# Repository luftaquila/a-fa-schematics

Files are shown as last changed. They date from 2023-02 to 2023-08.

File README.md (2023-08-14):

# E-Formula 전기시스템 파트 회로도 / PCB / 배선

상위 프로젝트: [luftaquila/a-fa-landing](https://github.com/luftaquila/a-fa-landing)



* 회로도  
    * *EV.kicad_pro*  
       * KiCAD 6.0 프로젝트  
       * 메인 회로도입니다. 추상적으로 차량의 모든 고전압/저전압 전기 계통이 표현되어 있습니다. 메인 회로도 하위의 계층 회로도는 개별 구성 요소를 추상화합니다. 계층 회로도 중 `/PCB` 폴더 하위의 파일들은 실제 PCB의 회로도입니다.

* PCB  
    * */PCB/\*.kicad_pcb*  
       * KiCAD 6.0 PCB 아트워크  
       * 각 PCB 폴더는 하나의 독립적인 KiCAD 프로젝트입니다. 메인 회로도인 `EV.kicad_sch` 파일이 계층 회로 구성을 통해 각 PCB 폴더의 `*.kicad_sch` 파일을 가리키는 방식으로 서로 연결되어 있습니다.

* 배선  
    * *wirings*
       * 차량의 모든 외부 배선을 표현하는 [WireViz](https://github.com/formatc1702/WireViz) 배선 체계도입니다.

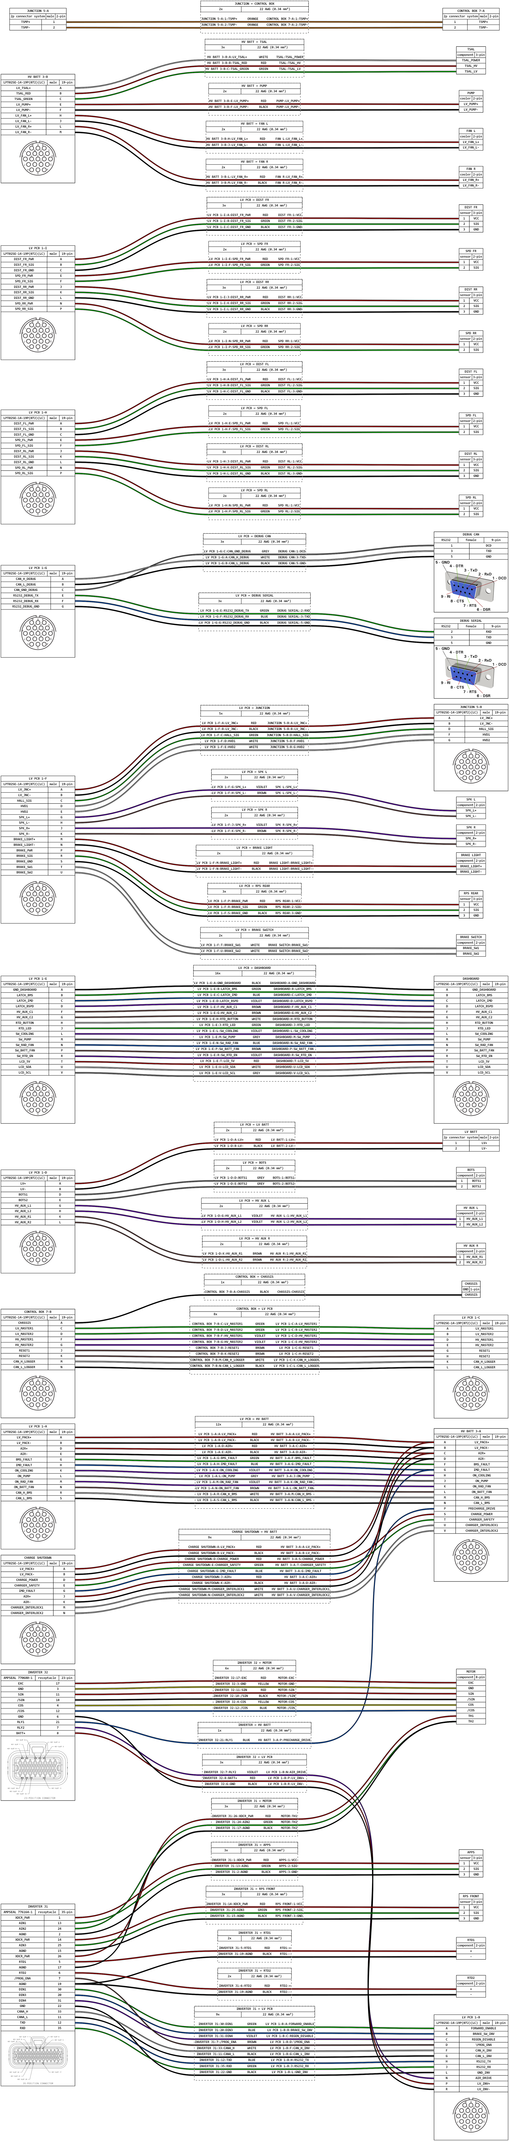
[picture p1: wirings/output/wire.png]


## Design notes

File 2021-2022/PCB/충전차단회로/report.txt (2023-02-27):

정보: 'C:\Users\kbc9513\Desktop\충전차단회로\충전차단회로.net' 네트리스트 파일을 읽고 있습니다.

정보: 참조 지정자를 사용하여 심볼과 풋프린트를 일치시킵니다.

정보: 심볼 'R1:Resistor_THT:R_Axial_DIN0207_L6.3mm_D2.5mm_P10.16mm_Horizontal' 처리 중입니다.
정보: 심볼 'R2:Resistor_THT:R_Axial_DIN0207_L6.3mm_D2.5mm_P10.16mm_Horizontal' 처리 중입니다.
정보: 심볼 'R3:Resistor_THT:R_Axial_DIN0207_L6.3mm_D2.5mm_P10.16mm_Horizontal' 처리 중입니다.
정보: 심볼 'D6:LED_THT:LED_D5.0mm' 처리 중입니다.
정보: 심볼 'J2:LED_THT:LED_D5.0mm' 처리 중입니다.
정보: 심볼 'R4:Resistor_THT:R_Axial_DIN0207_L6.3mm_D2.5mm_P10.16mm_Horizontal' 처리 중입니다.
정보: 심볼 'J3:LED_THT:LED_D5.0mm' 처리 중입니다.
정보: 심볼 'D3:LED_THT:LED_D5.0mm' 처리 중입니다.
정보: 심볼 'U1:Goolgle_Drive_Library:ADJ14012' 처리 중입니다.
정보: 심볼 'J1:LED_THT:LED_D5.0mm' 처리 중입니다.
정보: 심볼 'U2:Goolgle_Drive_Library:ADJ14012' 처리 중입니다.
정보: 심볼 'D1:Diode_THT:D_DO-15_P10.16mm_Horizontal' 처리 중입니다.
정보: 심볼 'D2:Diode_THT:D_DO-15_P10.16mm_Horizontal' 처리 중입니다.
정보: 심볼 'D4:Diode_THT:D_DO-15_P10.16mm_Horizontal' 처리 중입니다.
정보: 심볼 'D5:Diode_THT:D_DO-15_P10.16mm_Horizontal' 처리 중입니다.
정보: 심볼 'J4:Connector_Wire:SolderWire-0.75sqmm_1x02_P4.8mm_D1.25mm_OD2.3mm' 처리 중입니다.
정보: 심볼 'J5:Connector_JST:JST_EH_B10B-EH-A_1x10_P2.50mm_Vertical' 처리 중입니다.
네트 Net-(R1-Pad2)을(를) 추가합니다.
R1 핀 2을(를) Net-(R1-Pad2)에 연결했습니다.
R2이(가) 추가되었습니다 (풋프린트 'Resistor_THT:R_Axial_DIN0207_L6.3mm_D2.5mm_P10.16mm_Horizontal').
참조 지정자 REF**을(를) R2(으)로 변경하였습니다.
값 R2을(를) R_Axial_DIN0207_L6.3mm_D2.5mm_P10.16mm_Horizontal에서 500(으)로 변경하였습니다.
R2 심볼 관련성을 에서 /9cac4b8f-fc90-46aa-9ba6-c3c9f12e7e00(으)로 업데이트하였습니다.
R2 속성이 업데이트되었습니다.
네트 GND을(를) 추가합니다.
R2 핀 1을(를) GND에 연결했습니다.
R2 핀 2을(를) Net-(D3-Pad2)에 연결했습니다.
R3이(가) 추가되었습니다 (풋프린트 'Resistor_THT:R_Axial_DIN0207_L6.3mm_D2.5mm_P10.16mm_Horizontal').
참조 지정자 REF**을(를) R3(으)로 변경하였습니다.
값 R3을(를) R_Axial_DIN0207_L6.3mm_D2.5mm_P10.16mm_Horizontal에서 1.5k(으)로 변경하였습니다.
R3 심볼 관련성을 에서 /c4ed5e0d-1470-49a7-b4d8-6793531b15c6(으)로 업데이트하였습니다.
R3 속성이 업데이트되었습니다.
네트 Net-(D6-Pad2)을(를) 추가합니다.
R3 핀 1을(를) Net-(D6-Pad2)에 연결했습니다.
네트 Net-(R3-Pad2)을(를) 추가합니다.
R3 핀 2을(를) Net-(R3-Pad2)에 연결했습니다.
R4이(가) 추가되었습니다 (풋프린트 'Resistor_THT:R_Axial_DIN0207_L6.3mm_D2.5mm_P10.16mm_Horizontal').
참조 지정자 REF**을(를) R4(으)로 변경하였습니다.
값 R4을(를) R_Axial_DIN0207_L6.3mm_D2.5mm_P10.16mm_Horizontal에서 500(으)로 변경하였습니다.
R4 심볼 관련성을 에서 /f852aa6c-fee4-4d12-afd9-4db3451e35ae(으)로 업데이트하였습니다.
R4 속성이 업데이트되었습니다.
R4 핀 1을(를) GND에 연결했습니다.
R4 핀 2을(를) Net-(D6-Pad2)에 연결했습니다.
D3이(가) 추가되었습니다 (풋프린트 'LED_THT:LED_D5.0mm').
참조 지정자 REF**을(를) D3(으)로 변경하였습니다.
값 D3을(를) LED_D5.0mm에서 LED(으)로 변경하였습니다.
D3 심볼 관련성을 에서 /42a2bed2-408c-4340-bf5e-717f9ef794f6(으)로 업데이트하였습니다.
D3 속성이 업데이트되었습니다.
D3 핀 1을(를) GND에 연결했습니다.
D3 핀 2을(를) Net-(D3-Pad2)에 연결했습니다.
D6이(가) 추가되었습니다 (풋프린트 'LED_THT:LED_D5.0mm').
참조 지정자 REF**을(를) D6(으)로 변경하였습니다.
값 D6을(를) LED_D5.0mm에서 LED(으)로 변경하였습니다.
D6 심볼 관련성을 에서 /54d4ccdd-eadf-48c0-9c4d-c1c9c0573c55(으)로 업데이트하였습니다.
D6 속성이 업데이트되었습니다.
D6 핀 1을(를) GND에 연결했습니다.
D6 핀 2을(를) Net-(D6-Pad2)에 연결했습니다.
J1이(가) 추가되었습니다 (풋프린트 'LED_THT:LED_D5.0mm').
참조 지정자 REF**을(를) J1(으)로 변경하였습니다.
값 J1을(를) LED_D5.0mm에서 Push-Rotate(으)로 변경하였습니다.
J1 심볼 관련성을 에서 /b73f0b34-054d-4499-b93b-f1d81da21695(으)로 업데이트하였습니다.
J1 속성이 업데이트되었습니다.
네트 Net-(J1-Pad1)을(를) 추가합니다.
J1 핀 1을(를) Net-(J1-Pad1)에 연결했습니다.
네트 CHARGE_POWER을(를) 추가합니다.
J1 핀 2을(를) CHARGE_POWER에 연결했습니다.
J2이(가) 추가되었습니다 (풋프린트 'LED_THT:LED_D5.0mm').
참조 지정자 REF**을(를) J2(으)로 변경하였습니다.
값 J2을(를) LED_D5.0mm에서 Charging_Interlock(으)로 변경하였습니다.
J2 심볼 관련성을 에서 /5271f79e-a5a9-419a-907c-0455a139a4e2(으)로 업데이트하였습니다.
J2 속성이 업데이트되었습니다.
네트 Net-(J2-Pad1)을(를) 추가합니다.
J2 핀 1을(를) Net-(J2-Pad1)에 연결했습니다.
J2 핀 2을(를) Net-(J1-Pad1)에 연결했습니다.
J3이(가) 추가되었습니다 (풋프린트 'LED_THT:LED_D5.0mm').
참조 지정자 REF**을(를) J3(으)로 변경하였습니다.
값 J3을(를) LED_D5.0mm에서 reset(으)로 변경하였습니다.
J3 심볼 관련성을 에서 /431705a8-970b-4ff5-b043-d4baa9fe7a97(으)로 업데이트하였습니다.
J3 속성이 업데이트되었습니다.
네트 Reset_Button을(를) 추가합니다.
J3 핀 1을(를) Reset_Button에 연결했습니다.
J3 핀 2을(를) GND에 연결했습니다.
U1이(가) 추가되었습니다 (풋프린트 'Goolgle_Drive_Library:ADJ14012').
참조 지정자 REF**을(를) U1(으)로 변경하였습니다.
값 U1을(를) RELAY_ADJ_1C_PAN에서 ADJ14012(으)로 변경하였습니다.
U1 심볼 관련성을 에서 /4dad1e6b-5c80-4c11-8ad5-7b16562ecc74(으)로 업데이트하였습니다.
U1 속성이 업데이트되었습니다.
U1 핀 1을(를) CHARGE_POWER에 연결했습니다.
네트 IMD_FAULT을(를) 추가합니다.
U1 핀 9을(를) IMD_FAULT에 연결했습니다.
U1 핀 8을(를) Reset_Button에 연결했습니다.
네트 Net-(U1-Pad2)을(를) 추가합니다.
U1 핀 2을(를) Net-(U1-Pad2)에 연결했습니다.
U1 핀 6을(를) Net-(R1-Pad2)에 연결했습니다.
U1 핀 4을(를) Net-(J2-Pad1)에 연결했습니다.
R1이(가) 추가되었습니다 (풋프린트 'Resistor_THT:R_Axial_DIN0207_L6.3mm_D2.5mm_P10.16mm_Horizontal').
U2이(가) 추가되었습니다 (풋프린트 'Goolgle_Drive_Library:ADJ14012').
참조 지정자 REF**을(를) U2(으)로 변경하였습니다.
값 U2을(를) RELAY_ADJ_1C_PAN에서 ADJ14012(으)로 변경하였습니다.
U2 심볼 관련성을 에서 /b592de20-0538-4c3f-838d-1e2c5cb1cc5b(으)로 업데이트하였습니다.
U2 속성이 업데이트되었습니다.
U2 핀 1을(를) CHARGE_POWER에 연결했습니다.
네트 CHARGE_SAFETY을(를) 추가합니다.
U2 핀 9을(를) CHARGE_SAFETY에 연결했습니다.
U2 핀 8을(를) Reset_Button에 연결했습니다.
네트 AIR+_ACTIVE을(를) 추가합니다.
U2 핀 2을(를) AIR+_ACTIVE에 연결했습니다.
U2 핀 6을(를) Net-(R3-Pad2)에 연결했습니다.
U2 핀 4을(를) Net-(U1-Pad2)에 연결했습니다.
참조 지정자 REF**을(를) R1(으)로 변경하였습니다.
D1이(가) 추가되었습니다 (풋프린트 'Diode_THT:D_DO-15_P10.16mm_Horizontal').
참조 지정자 REF**을(를) D1(으)로 변경하였습니다.
값 D1을(를) D_DO-15_P10.16mm_Horizontal에서 1N4001(으)로 변경하였습니다.
D1 심볼 관련성을 에서 /04f6e974-f1aa-4eba-86e4-b6ef5f9aab0c(으)로 업데이트하였습니다.
D1 속성이 업데이트되었습니다.
D1 핀 1을(를) CHARGE_POWER에 연결했습니다.
D1 핀 2을(를) Reset_Button에 연결했습니다.
값 R1을(를) R_Axial_DIN0207_L6.3mm_D2.5mm_P10.16mm_Horizontal에서 1.5k(으)로 변경하였습니다.
D2이(가) 추가되었습니다 (풋프린트 'Diode_THT:D_DO-15_P10.16mm_Horizontal').
참조 지정자 REF**을(를) D2(으)로 변경하였습니다.
값 D2을(를) D_DO-15_P10.16mm_Horizontal에서 1N4001(으)로 변경하였습니다.
D2 심볼 관련성을 에서 /54878bf1-8f32-4bae-9656-436220390256(으)로 업데이트하였습니다.
D2 속성이 업데이트되었습니다.
D2 핀 1을(를) CHARGE_POWER에 연결했습니다.
D2 핀 2을(를) IMD_FAULT에 연결했습니다.
R1 심볼 관련성을 에서 /6292f032-e986-4e86-8de2-ea34f8531d00(으)로 업데이트하였습니다.
D4이(가) 추가되었습니다 (풋프린트 'Diode_THT:D_DO-15_P10.16mm_Horizontal').
참조 지정자 REF**을(를) D4(으)로 변경하였습니다.
값 D4을(를) D_DO-15_P10.16mm_Horizontal에서 1N4001(으)로 변경하였습니다.
D4 심볼 관련성을 에서 /92f338f3-3812-48b7-a538-72a2acf5d354(으)로 업데이트하였습니다.
D4 속성이 업데이트되었습니다.
D4 핀 1을(를) CHARGE_POWER에 연결했습니다.
D4 핀 2을(를) Reset_Button에 연결했습니다.
R1 속성이 업데이트되었습니다.
D5이(가) 추가되었습니다 (풋프린트 'Diode_THT:D_DO-15_P10.16mm_Horizontal').
참조 지정자 REF**을(를) D5(으)로 변경하였습니다.
값 D5을(를) D_DO-15_P10.16mm_Horizontal에서 1N4001(으)로 변경하였습니다.
D5 심볼 관련성을 에서 /d5f5c3b9-1b42-4bee-8aa3-7b56f2060ad2(으)로 업데이트하였습니다.
D5 속성이 업데이트되었습니다.
D5 핀 1을(를) CHARGE_POWER에 연결했습니다.
D5 핀 2을(를) CHARGE_SAFETY에 연결했습니다.
네트 Net-(D3-Pad2)을(를) 추가합니다.
J4이(가) 추가되었습니다 (풋프린트 'Connector_Wire:SolderWire-0.75sqmm_1x02_P4.8mm_D1.25mm_OD2.3mm').
참조 지정자 REF**을(를) J4(으)로 변경하였습니다.
값 J4을(를) SolderWire-0.75sqmm_1x02_P4.8mm_D1.25mm_OD2.3mm에서 SMPS INPUT(으)로 변경하였습니다.
J4 심볼 관련성을 에서 /914a5bc4-e45f-4260-9574-6d60e49f788f(으)로 업데이트하였습니다.
J4 속성이 업데이트되었습니다.
J4에 'BOM에서 제외' 제작 속성이 제거되었습니다.
J4 핀 1을(를) CHARGE_POWER에 연결했습니다.
J4 핀 2을(를) GND에 연결했습니다.
R1 핀 1을(를) Net-(D3-Pad2)에 연결했습니다.
J5이(가) 추가되었습니다 (풋프린트 'Connector_JST:JST_EH_B10B-EH-A_1x10_P2.50mm_Vertical').
참조 지정자 REF**을(를) J5(으)로 변경하였습니다.
값 J5을(를) JST_EH_B10B-EH-A_1x10_P2.50mm_Vertical에서 Conn_01x10_Male(으)로 변경하였습니다.
J5 심볼 관련성을 에서 /5f07ac3b-b444-4c3e-bbea-05685bee6cad(으)로 업데이트하였습니다.
J5 속성이 업데이트되었습니다.
J5 핀 1을(를) CHARGE_POWER에 연결했습니다.
J5 핀 2을(를) GND에 연결했습니다.
J5 핀 3을(를) IMD_FAULT에 연결했습니다.
J5 핀 4을(를) AIR+_ACTIVE에 연결했습니다.
J5 핀 5을(를) AIR+_ACTIVE에 연결했습니다.
네트 unconnected-(J5-Pad6)을(를) 추가합니다.
J5 핀 6을(를) unconnected-(J5-Pad6)에 연결했습니다.
네트 unconnected-(J5-Pad7)을(를) 추가합니다.
J5 핀 7을(를) unconnected-(J5-Pad7)에 연결했습니다.
J5 핀 8을(를) CHARGE_POWER에 연결했습니다.
J5 핀 9을(를) CHARGE_SAFETY에 연결했습니다.
J5 핀 10을(를) GND에 연결했습니다.

정보: 총 경고: 0개, 오류: 0개.

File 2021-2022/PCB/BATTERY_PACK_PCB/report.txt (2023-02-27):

1k이(가) R18(으)로 주석 처리되었습니다.
부품 참조번호 주석 처리가 완료되었습니다.

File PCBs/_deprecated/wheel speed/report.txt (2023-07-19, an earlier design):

Info: Processing symbol 'C1:Capacitor_THT:C_Disc_D5.0mm_W2.5mm_P2.50mm'.
Info: Processing symbol 'C2:Capacitor_THT:C_Disc_D5.0mm_W2.5mm_P2.50mm'.
Info: Processing symbol 'C3:Capacitor_THT:C_Disc_D5.0mm_W2.5mm_P2.50mm'.
Info: Processing symbol 'C4:Capacitor_THT:C_Disc_D5.0mm_W2.5mm_P2.50mm'.
Info: Processing symbol 'J1:Connector_PinHeader_2.54mm:PinHeader_1x02_P2.54mm_Vertical'.
Info: Processing symbol 'J2:Connector_PinHeader_2.54mm:PinHeader_1x04_P2.54mm_Vertical'.
Info: Processing symbol 'J3:Connector_PinHeader_2.54mm:PinHeader_1x08_P2.54mm_Vertical'.
Info: Processing symbol 'R1:Resistor_THT:R_Axial_DIN0204_L3.6mm_D1.6mm_P5.08mm_Horizontal'.
Info: Processing symbol 'R2:Resistor_THT:R_Axial_DIN0204_L3.6mm_D1.6mm_P5.08mm_Horizontal'.
Info: Processing symbol 'R3:Resistor_THT:R_Axial_DIN0204_L3.6mm_D1.6mm_P5.08mm_Horizontal'.
Info: Processing symbol 'R4:Resistor_THT:R_Axial_DIN0204_L3.6mm_D1.6mm_P5.08mm_Horizontal'.
Info: Processing symbol 'R5:Resistor_THT:R_Axial_DIN0204_L3.6mm_D1.6mm_P5.08mm_Horizontal'.
Info: Processing symbol 'R6:Resistor_THT:R_Axial_DIN0204_L3.6mm_D1.6mm_P5.08mm_Horizontal'.
Info: Processing symbol 'R7:Resistor_THT:R_Axial_DIN0204_L3.6mm_D1.6mm_P5.08mm_Horizontal'.
Info: Processing symbol 'R8:Resistor_THT:R_Axial_DIN0204_L3.6mm_D1.6mm_P5.08mm_Horizontal'.
Info: Processing symbol 'R9:Resistor_THT:R_Axial_DIN0204_L3.6mm_D1.6mm_P5.08mm_Horizontal'.
Info: Processing symbol 'R10:Resistor_THT:R_Axial_DIN0204_L3.6mm_D1.6mm_P5.08mm_Horizontal'.
Info: Processing symbol 'R11:Resistor_THT:R_Axial_DIN0204_L3.6mm_D1.6mm_P5.08mm_Horizontal'.
Info: Processing symbol 'R12:Resistor_THT:R_Axial_DIN0204_L3.6mm_D1.6mm_P5.08mm_Horizontal'.
Info: Processing symbol 'U1:footprint:AMS1117-5.0'.
Info: Processing symbol 'U2:footprint:AMS1117-5.0'.
Info: Processing symbol 'U3:footprint:LM311P'.
Info: Processing symbol 'U4:footprint:LM311P'.
Info: Processing symbol 'U5:footprint:LM311P'.
Info: Processing symbol 'U6:footprint:LM311P'.
Changed C1 footprint from 'Capacitor_THT:C_Disc_D5.1mm_W3.2mm_P5.00mm' to 'Capacitor_THT:C_Disc_D5.0mm_W2.5mm_P2.50mm'.
Changed C2 footprint from 'Capacitor_THT:C_Disc_D5.1mm_W3.2mm_P5.00mm' to 'Capacitor_THT:C_Disc_D5.0mm_W2.5mm_P2.50mm'.
Changed C3 footprint from 'Capacitor_THT:C_Disc_D5.1mm_W3.2mm_P5.00mm' to 'Capacitor_THT:C_Disc_D5.0mm_W2.5mm_P2.50mm'.
Changed C4 footprint from 'Capacitor_THT:C_Disc_D5.1mm_W3.2mm_P5.00mm' to 'Capacitor_THT:C_Disc_D5.0mm_W2.5mm_P2.50mm'.
Warning: No net found for symbol U1 pin 4.
Warning: No net found for symbol U2 pin 4.

Info: Total warnings: 0, errors: 0.

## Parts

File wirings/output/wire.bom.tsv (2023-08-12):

Id | Description | Qty | Unit | Designators
1 | Connector, 2p connector system, male, 2 pins | 2 |  | CONTROL BOX 7-A, JUNCTION 5-A
2 | Connector, AMPSEAL 770680-1, receptacle, 23 pins | 1 |  | INVERTER J2
3 | Connector, AMPSEAL 776164-1, receptacle, 35 pins | 1 |  | INVERTER J1
4 | Connector, GND, 1 pins | 1 |  | CHASSIS
5 | Connector, LPT02SE-14-19P(072)(LC), male, 19 pins | 14 |  | CHARGE SHUTDOWN A, CONTROL BOX 7-B, DASHBOARD, HV BATT 3-A, HV BATT 3-B, JUNCTION 5-B, LV PCB 1-A, LV PCB 1-B, LV PCB 1-C, LV PCB 1-E, LV PCB 1-F, LV PCB 1-G, LV PCB 1-H, LV PCB 1-I
6 | Connector, RS232, female, 9 pins | 3 |  | CHARGE SHUTDOWN B, DEBUG CAN, DEBUG SERIAL
7 | Connector, component, 2 pins | 9 |  | BOTS, BRAKE LIGHT, BRAKE SWITCH, HV AUX L, HV AUX R, RTD1, RTD2, SPK L, SPK R
8 | Connector, component, 3 pins | 1 |  | TSAL
9 | Connector, component, 8 pins | 1 |  | MOTOR
10 | Connector, cooler, 2 pins | 3 |  | FAN L, FAN R, PUMP
11 | Connector, jumper, 4 pins | 1 |  | DEBUG UART
12 | Connector, sensor, 2 pins | 4 |  | SPD FL, SPD FR, SPD RL, SPD RR
13 | Connector, sensor, 3 pins | 7 |  | APPS, DIST FL, DIST FR, DIST RL, DIST RR, RPS FRONT, RPS REAR
14 | Wire, 18 AWG, BLACK | 0 | m | CONTROL BOX ↔ CHASSIS, HV BATT ↔ PUMP
15 | Wire, 18 AWG, GREEN | 0 | m | HV BATT ↔ FAN L, HV BATT ↔ FAN R
16 | Wire, 18 AWG, RED | 0 | m | HV BATT ↔ PUMP, LV PCB ↔ BOTS, LV PCB ↔ HV AUX L, LV PCB ↔ HV AUX R
17 | Wire, 18 AWG, YELLOW | 0 | m | HV BATT ↔ FAN L, HV BATT ↔ FAN R
18 | Wire, 22 AWG, BLACK | 0 | m | CHARGE DEBUG CAN ↔ HV BATT, INVERTER J1 ↔ LV PCB, INVERTER J1 ↔ RTD1, INVERTER J1 ↔ RTD2, INVERTER J2 ↔ LV PCB, INVERTER J2 ↔ MOTOR, LV PCB ↔ BRAKE LIGHT, LV PCB ↔ DEBUG CAN, LV PCB ↔ DEBUG SERIAL, LV PCB ↔ DEBUG UART, LV PCB ↔ RPS REAR, LV PCB ↔ SPD FL, LV PCB ↔ SPD FR, LV PCB ↔ SPD RL, LV PCB ↔ SPD RR
19 | Wire, 22 AWG, BLUE | 0 | m | INVERTER J1 ↔ LV PCB, INVERTER J2 ↔ MOTOR, INVERTER ↔ HV BATT, LV PCB ↔ DEBUG SERIAL, LV PCB ↔ DEBUG UART
20 | Wire, 22 AWG, BROWN | 0 | m | INVERTER J1 ↔ LV PCB, INVERTER J1 ↔ MOTOR, INVERTER J2 ↔ MOTOR
21 | Wire, 22 AWG, GREEN | 0 | m | HV BATT ↔ TSAL, INVERTER J1 ↔ APPS, INVERTER J1 ↔ LV PCB, INVERTER J1 ↔ RPS FRONT, INVERTER J2 ↔ MOTOR, LV PCB ↔ DEBUG SERIAL, LV PCB ↔ DIST FL, LV PCB ↔ DIST FR, LV PCB ↔ DIST RL, LV PCB ↔ DIST RR, LV PCB ↔ RPS REAR
22 | Wire, 22 AWG, GREY | 0 | m | INVERTER J1 ↔ APPS, INVERTER J1 ↔ RPS FRONT, INVERTER J2 ↔ MOTOR, LV PCB ↔ DEBUG CAN, LV PCB ↔ DIST FL, LV PCB ↔ DIST FR, LV PCB ↔ DIST RL, LV PCB ↔ DIST RR, LV PCB ↔ SPK L, LV PCB ↔ SPK R
23 | Wire, 22 AWG, ORANGE | 0 | m | JUNCTION ↔ CONTROL BOX
24 | Wire, 22 AWG, RED | 0 | m | HV BATT ↔ TSAL, INVERTER J1 ↔ APPS, INVERTER J1 ↔ LV PCB, INVERTER J1 ↔ MOTOR, INVERTER J1 ↔ RPS FRONT, INVERTER J1 ↔ RTD1, INVERTER J1 ↔ RTD2, INVERTER J2 ↔ LV PCB, INVERTER J2 ↔ MOTOR, LV PCB ↔ BRAKE LIGHT, LV PCB ↔ DIST FL, LV PCB ↔ DIST FR, LV PCB ↔ DIST RL, LV PCB ↔ DIST RR, LV PCB ↔ RPS REAR, LV PCB ↔ SPD FL, LV PCB ↔ SPD FR, LV PCB ↔ SPD RL, LV PCB ↔ SPD RR
25 | Wire, 22 AWG, VIOLET | 0 | m | HV BATT ↔ TSAL, INVERTER J1 ↔ LV PCB, INVERTER J2 ↔ LV PCB, LV PCB ↔ BRAKE SWITCH, LV PCB ↔ SPK L, LV PCB ↔ SPK R
26 | Wire, 22 AWG, WHITE | 0 | m | CHARGE DEBUG CAN ↔ HV BATT, INVERTER J1 ↔ LV PCB, LV PCB ↔ BRAKE SWITCH, LV PCB ↔ DEBUG CAN, LV PCB ↔ DEBUG UART
27 | Wire, BLACK | 0 | m | CHARGE SHUTDOWN ↔ HV BATT, CONTROL BOX ↔ LV PCB, LV PCB ↔ DASHBOARD, LV PCB ↔ HV BATT, LV PCB ↔ JUNCTION
28 | Wire, BLUE | 0 | m | CHARGE SHUTDOWN ↔ HV BATT, LV PCB ↔ DASHBOARD, LV PCB ↔ HV BATT
29 | Wire, BROWN | 0 | m | CONTROL BOX ↔ LV PCB, LV PCB ↔ DASHBOARD, LV PCB ↔ HV BATT
30 | Wire, GREEN | 0 | m | CHARGE SHUTDOWN ↔ HV BATT, LV PCB ↔ DASHBOARD, LV PCB ↔ HV BATT, LV PCB ↔ JUNCTION
31 | Wire, GREY | 0 | m | LV PCB ↔ DASHBOARD, LV PCB ↔ HV BATT
32 | Wire, RED | 0 | m | CHARGE SHUTDOWN ↔ HV BATT, CONTROL BOX ↔ LV PCB, LV PCB ↔ DASHBOARD, LV PCB ↔ HV BATT, LV PCB ↔ JUNCTION
33 | Wire, VIOLET | 0 | m | LV PCB ↔ DASHBOARD, LV PCB ↔ HV BATT
34 | Wire, WHITE | 0 | m | CHARGE SHUTDOWN ↔ HV BATT, CONTROL BOX ↔ LV PCB, LV PCB ↔ DASHBOARD, LV PCB ↔ HV BATT, LV PCB ↔ JUNCTION

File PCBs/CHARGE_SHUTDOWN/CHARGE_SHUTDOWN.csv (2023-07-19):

Source: | G:\Shared drives\A-FA E-포뮬러 전기시스템\회로 및 PCB\PCBs\CHARGE_SHUTDOWN\CHARGE_SHUTDOWN.kicad_sch
Date: | 2023-07-09 오후 3:33:17
Tool: | Eeschema (6.0.8)
Generator: | C:\Program Files\KiCad\6.0\bin\scripting\plugins/bom_csv_grouped_by_value_with_fp.py
Component Count: | 29
Ref | Qnty | Value | Cmp name | Footprint | Description | Vendor
D1, | 1 | LV_ACTIVE_LED | LED | LED_THT:LED_D5.0mm | Light emitting diode
D2, | 1 | SWITCH_ACTIVE_LED | LED | LED_THT:LED_D5.0mm | Light emitting diode
D3, D5, | 2 | LED_RED | LED | LED_THT:LED_D5.0mm | Light emitting diode
D4, | 1 | IMD_RED | LED | LED_THT:LED_D5.0mm | Light emitting diode
D6, | 1 | BMS_RED | LED | LED_THT:LED_D5.0mm | Light emitting diode
D7, | 1 | AIR_ACTIVE_LED | LED | LED_THT:LED_D5.0mm | Light emitting diode
J1, | 1 | PUSH_ROTATE | Conn_01x02_Male | Connector_PinHeader_2.54mm:PinHeader_1x02_P2.54mm_Vertical | Generic connector, single row, 01x02, script generated (kicad-library-utils/schlib/autogen/connector/)
J2, | 1 | PACK | Conn_01x12_Male | Connector_PinHeader_2.54mm:PinHeader_1x12_P2.54mm_Vertical | Generic connector, single row, 01x12, script generated (kicad-library-utils/schlib/autogen/connector/)
J3, | 1 | SMPS | Conn_01x02_Male | Connector_PinHeader_2.54mm:PinHeader_1x02_P2.54mm_Vertical | Generic connector, single row, 01x02, script generated (kicad-library-utils/schlib/autogen/connector/)
J4, | 1 | RESET | Conn_01x02_Male | Connector_PinHeader_2.54mm:PinHeader_1x02_P2.54mm_Vertical | Generic connector, single row, 01x02, script generated (kicad-library-utils/schlib/autogen/connector/)
J5, | 1 | HV | Conn_01x02_Male | Connector_PinHeader_2.54mm:PinHeader_1x02_P2.54mm_Vertical | Generic connector, single row, 01x02, script generated (kicad-library-utils/schlib/autogen/connector/)
J6, | 1 | AC_RELAY | Conn_01x02_Male | Connector_PinHeader_2.54mm:PinHeader_1x02_P2.54mm_Vertical | Generic connector, single row, 01x02, script generated (kicad-library-utils/schlib/autogen/connector/)
J7, | 1 | Conn_01x01_Female | Conn_01x01_Female | Connector:Banana_Jack_1Pin | Generic connector, single row, 01x01, script generated (kicad-library-utils/schlib/autogen/connector/)
Q1, | 1 | IRF9540N | IRF9540N | Package_TO_SOT_THT:TO-220-3_Vertical | -23A Id, -100V Vds, 117mOhm Rds, P-Channel HEXFET Power MOSFET, TO-220
Q2, | 1 | IRF740 | IRF740 | Package_TO_SOT_THT:TO-220-3_Vertical | 10A Id, 400V Vds, N-Channel Power MOSFET, 500mOhm Rds, TO-220AB
R1, R2, R3, R4, R6, R7, | 6 | 10k | R_US | Resistor_THT:R_Axial_DIN0204_L3.6mm_D1.6mm_P7.62mm_Horizontal | Resistor, US symbol
R5, | 1 | 240K | R_US | Resistor_THT:R_Axial_DIN0204_L3.6mm_D1.6mm_P7.62mm_Horizontal | Resistor, US symbol
R8, R9, | 2 | 10K | R | Resistor_THT:R_Axial_DIN0922_L20.0mm_D9.0mm_P30.48mm_Horizontal | Resistor
R_DIS1, | 1 | 1k | Heater | footprint:HSC100 | Resistive heater
RELAY_DISCHARGE1, | 1 | G2RL-1_12DC | G2RL-1_12DC | footprint:G2RL112DC | General Purpose Relay, G2RL Series, Power, Non Latching, SPDT, 12 VDC, 12 A RoHS Compliant: Yes
U1, U2, | 2 | ADJ14012 | ADJ14024 | footprints:ADJ14024

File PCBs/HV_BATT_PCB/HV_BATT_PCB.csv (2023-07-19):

Source: | G:\Shared drives\A-FA E-포뮬러 전기시스템\회로 및 PCB\PCBs\HV_BATT_PCB\HV_BATT_PCB.kicad_sch
Date: | 2023-07-09 오후 4:16:06
Tool: | Eeschema (6.0.8)
Generator: | C:\Program Files\KiCad\6.0\bin\scripting\plugins/bom_csv_grouped_by_value_with_fp.py
Component Count: | 66
Ref | Qnty | Value | Cmp name | Footprint | Description | Vendor
asdf1, | 1 | Conn_01x10_Male | Conn_01x10_Male | Connector_Molex:Molex_Micro-Fit_3.0_43650-1015_1x10_P3.00mm_Vertical | Generic connector, single row, 01x10, script generated (kicad-library-utils/schlib/autogen/connector/)
BMS1, | 1 | Conn_01x08_Male | Conn_01x08_Male | Connector_PinHeader_2.54mm:PinHeader_1x08_P2.54mm_Vertical | Generic connector, single row, 01x08, script generated (kicad-library-utils/schlib/autogen/connector/)
C1, C2, | 2 | 2.2uF | C | Capacitor_THT:CP_Radial_D8.0mm_P5.00mm | Unpolarized capacitor
C3, | 1 | 1nF | C_Small | Capacitor_THT:C_Disc_D4.3mm_W1.9mm_P5.00mm | Unpolarized capacitor, small symbol
C4, | 1 | 1uF | C_Small | Capacitor_THT:C_Disc_D4.3mm_W1.9mm_P5.00mm | Unpolarized capacitor, small symbol
C5, | 1 | 1uF | C | Capacitor_THT:C_Axial_L3.8mm_D2.6mm_P15.00mm_Horizontal | Unpolarized capacitor
C6, | 1 | 1uF | C_Polarized | Capacitor_THT:CP_Radial_D8.0mm_P5.00mm | Polarized capacitor
D1, D2, D4, D5, D6, D7, | 6 | 1N5349 | 1N53xxB | Diode_THT:D_DO-15_P10.16mm_Horizontal | 5000mW Zener Diode, DO-201
D3, | 1 | TVS | 1.5KExxA | Diode_SMD:D_SMC | 1500W unidirectional TRANSZORB® Transient Voltage Suppressor, DO-201AE
dff1, | 1 | Conn_01x14_Male | Conn_01x14_Male | Connector_PinHeader_2.54mm:PinHeader_1x14_P2.54mm_Vertical | Generic connector, single row, 01x14, script generated (kicad-library-utils/schlib/autogen/connector/)
F1, | 1 | SMCJ440A | Fuse | Fuse:Fuseholder_Cylinder-5x20mm_Schurter_0031_8201_Horizontal_Open | Fuse
F2, | 1 | 1A Fuse | Fuse | Fuse:Fuseholder_Cylinder-5x20mm_Schurter_0031_8201_Horizontal_Open | Fuse
F3, | 1 | 3A Fuse | Fuse | Fuse:Fuseholder_Cylinder-5x20mm_Schurter_0031_8201_Horizontal_Open | Fuse
FAN,GND_{AIR1, | 1 | Conn_01x04_Male | Conn_01x04_Male | Connector_PinHeader_2.54mm:PinHeader_1x04_P2.54mm_Vertical | Generic connector, single row, 01x04, script generated (kicad-library-utils/schlib/autogen/connector/)
HV_{PCB1, | 1 | Conn_01x02_Male | Conn_01x02_Male | Connector_Molex:Molex_Micro-Fit_3.0_43650-0215_1x02_P3.00mm_Vertical | Generic connector, single row, 01x02, script generated (kicad-library-utils/schlib/autogen/connector/)
IMD1, | 1 | Conn_01x06_Male | Conn_01x06_Male | Connector_PinHeader_2.54mm:PinHeader_1x06_P2.54mm_Vertical | Generic connector, single row, 01x06, script generated (kicad-library-utils/schlib/autogen/connector/)
J1, | 1 | Conn_01x02_Male | Conn_01x02_Male | Connector_Molex:Molex_Micro-Fit_3.0_43650-0215_1x02_P3.00mm_Vertical | Generic connector, single row, 01x02, script generated (kicad-library-utils/schlib/autogen/connector/)
K1, | 1 | PUMP | DIPxx-1Cxx-51x | Goolgle_Drive_Library:HR702 | Standex Meder DIP reed relay, SPDT
K2, | 1 | FAN_R | DIPxx-1Cxx-51x | Goolgle_Drive_Library:HR702 | Standex Meder DIP reed relay, SPDT
K3, | 1 | FAN_L | DIPxx-1Cxx-51x | Goolgle_Drive_Library:HR702 | Standex Meder DIP reed relay, SPDT
K4, | 1 | LV_BATT_FAN | DIPxx-1Cxx-51x | Goolgle_Drive_Library:HR702 | Standex Meder DIP reed relay, SPDT
PRECHARGE1, | 1 | G2RL-1_12DC | G2RL-1_12DC | Goolgle_Drive_Library:G2RL112DC | General Purpose Relay, G2RL Series, Power, Non Latching, SPDT, 12 VDC, 12 A RoHS Compliant: Yes
PRECHARGE2, | 1 | Conn_01x02_Male | Conn_01x02_Male | Connector_Molex:Molex_Micro-Fit_3.0_43650-0215_1x02_P3.00mm_Vertical | Generic connector, single row, 01x02, script generated (kicad-library-utils/schlib/autogen/connector/)
PS1, | 1 | SPAN02A-12 | SPAN02A-12 | Goolgle_Drive_Library:SPAN02A12 | Isolated DC/DC Converters 9-18Vin 12Vout 167mA SIP8 Reg Iso
PS2, | 1 | QHL300300S12 | QHL300300S12 | Goolgle_Drive_Library:QHL300300S28
Q1, Q2, Q3, | 3 | IRF640 | Q_NMOS_GDS | Goolgle_Drive_Library:IRF640NPBF | N-MOSFET transistor, gate/drain/source
R1, R2, R3, R4, R6, R7, R9, R11, | 8 | 4.7M | R_US | Resistor_THT:R_Axial_DIN0207_L6.3mm_D2.5mm_P10.16mm_Horizontal | Resistor, US symbol
R5, | 1 | 1M | R_US | Resistor_THT:R_Axial_DIN0207_L6.3mm_D2.5mm_P10.16mm_Horizontal | Resistor, US symbol
R8, | 1 | 390k | R_US | Resistor_THT:R_Axial_DIN0207_L6.3mm_D2.5mm_P10.16mm_Horizontal | Resistor, US symbol
R10, | 1 | 4.7k | R_US | Resistor_THT:R_Axial_DIN0207_L6.3mm_D2.5mm_P10.16mm_Horizontal | Resistor, US symbol
R12, | 1 | 18k | R_US | Resistor_THT:R_Axial_DIN0207_L6.3mm_D2.5mm_P10.16mm_Horizontal | Resistor, US symbol
R13, | 1 | 12k | R_US | Resistor_THT:R_Axial_DIN0207_L6.3mm_D2.5mm_P10.16mm_Horizontal | Resistor, US symbol
R14, R18, | 2 | 10k | R_US | Resistor_THT:R_Axial_DIN0207_L6.3mm_D2.5mm_P10.16mm_Horizontal | Resistor, US symbol
R15, R19, | 2 | 2k2 | R_US | Resistor_THT:R_Axial_DIN0207_L6.3mm_D2.5mm_P10.16mm_Horizontal | Resistor, US symbol
R16, | 1 | 1k | R_US | Resistor_THT:R_Axial_DIN0207_L6.3mm_D2.5mm_P10.16mm_Horizontal | Resistor, US symbol
R17, | 1 | 100k | R_US | Resistor_THT:R_Axial_DIN0207_L6.3mm_D2.5mm_P10.16mm_Horizontal | Resistor, US symbol
R20, R21, | 2 | 240k | R_US | Resistor_THT:R_Axial_DIN0207_L6.3mm_D2.5mm_P10.16mm_Horizontal | Resistor, US symbol
TEMP1, | 1 | Conn_01x02_Male | Conn_01x02_Male | Connector_PinHeader_2.54mm:PinHeader_2x01_P2.54mm_Vertical | Generic connector, single row, 01x02, script generated (kicad-library-utils/schlib/autogen/connector/)
U1, U2, U3, U4, U5, U7, | 6 | LR8 | LR8K4-G | Goolgle_Drive_Library:LR8N3-G | 30mA 450V High-Voltage Linear Regulator (Adjustable), TO-252 (D-PAK)
U6, | 1 | LM311 | LM311 | Goolgle_Drive_Library:LM311P | Voltage Comparator, DIP-8/SOIC-8
U8, | 1 | 4N35 | 4N35 | Goolgle_Drive_Library:4N35 | Optocoupler, Phototransistor Output, with Base Connection, Vce 70V, CTR 100%, Viso 5000V, DIP6
U9, | 1 | NE555P | NE555P | Goolgle_Drive_Library:NE555P | Precision Timers, 555 compatible, PDIP-8
VI1, | 1 | Conn_01x02_Male | Conn_01x02_Male | Connector_PinHeader_2.54mm:PinHeader_2x01_P2.54mm_Vertical | Generic connector, single row, 01x02, script generated (kicad-library-utils/schlib/autogen/connector/)

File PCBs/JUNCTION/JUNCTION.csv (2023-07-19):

Source: | G:\Shared drives\A-FA E-포뮬러 전기시스템\회로 및 PCB\PCBs\JUNCTION\JUNCTION.kicad_sch
Date: | 2023-07-09 오후 3:49:55
Tool: | Eeschema (6.0.8)
Generator: | C:\Program Files\KiCad\6.0\bin\scripting\plugins/bom_csv_grouped_by_value_with_fp.py
Component Count: | 12
Ref | Qnty | Value | Cmp name | Footprint | Description | Vendor
J1, | 1 | JUNC | Conn_01x06_Female | Connector_PinHeader_2.54mm:PinHeader_1x06_P2.54mm_Vertical
J2, | 1 | TSMP | Conn_01x02_Female | Connector_Molex:Molex_Micro-Fit_3.0_43650-0215_1x02_P3.00mm_Vertical | Generic connector, single row, 01x02, script generated (kicad-library-utils/schlib/autogen/connector/)
J3, | 1 | HV | Conn_01x02_Female | Connector_Molex:Molex_Micro-Fit_3.0_43650-0215_1x02_P3.00mm_Vertical | Generic connector, single row, 01x02, script generated (kicad-library-utils/schlib/autogen/connector/)
J4, | 1 | HVD_IN | Conn_01x02_Female | Connector_PinHeader_2.54mm:PinHeader_1x02_P2.54mm_Vertical | Generic connector, single row, 01x02, script generated (kicad-library-utils/schlib/autogen/connector/)
J5, | 1 | HALL | Conn_01x03_Female | Connector_PinHeader_2.54mm:PinHeader_1x03_P2.54mm_Vertical
J6, | 1 | ENERGYMETER | Conn_01x02_Female | Connector_PinHeader_2.54mm:PinHeader_1x02_P2.54mm_Vertical | Generic connector, single row, 01x02, script generated (kicad-library-utils/schlib/autogen/connector/)
J7, | 1 | R_DISCHARGE | Conn_01x01_Female | Connector_PinHeader_2.54mm:PinHeader_1x01_P2.54mm_Vertical | Generic connector, single row, 01x01, script generated (kicad-library-utils/schlib/autogen/connector/)
R1, R2, | 2 | 10k | R_US | Resistor_THT:R_Axial_DIN0922_L20.0mm_D9.0mm_P30.48mm_Horizontal | Resistor, US symbol
R_DIS_place_in_pcb1, | 1 | 1k | Heater | footprint:HSC100 | Resistive heater
RELAY_DISCHARGE1, | 1 | G2RL-1_12DC | G2RL-1_12DC | footprint:G2RL112DC | General Purpose Relay, G2RL Series, Power, Non Latching, SPDT, 12 VDC, 12 A RoHS Compliant: Yes
U1, | 1 | AMS1117-5.0 | AMS1117-5.0 | footprint:AMS1117-5.0 | 1A Low Dropout regulator, positive, 5.0V fixed output, SOT-223

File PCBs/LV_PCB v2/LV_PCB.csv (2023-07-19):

Source: | G:\Shared drives\A-FA E-포뮬러 전기시스템\회로 및 PCB\PCBs\LV_PCB\LV_PCB.kicad_sch
Date: | 2023-07-09 오후 6:42:02
Tool: | Eeschema (6.0.8)
Generator: | C:\Program Files\KiCad\6.0\bin\scripting\plugins/bom_csv_grouped_by_value_with_fp.py
Component Count: | 143
Ref | Qnty | Value | Cmp name | Footprint | Description | Vendor
10uF1, | 1 | 10uF | C_Polarized | Capacitor_THT:CP_Radial_D5.0mm_P2.50mm | Polarized capacitor
AE1, | 1 | GPS | Antenna | footprint:ANTENA | Antenna
C1, C2, C3, C4, | 4 | 1nF | C_Small | Capacitor_THT:C_Disc_D5.0mm_W2.5mm_P2.50mm | Unpolarized capacitor, small symbol
C5, C6, | 2 | 100uF | C_Polarized_Small | Capacitor_THT:CP_Radial_D5.0mm_P2.50mm | Polarized capacitor, small symbol
D1, | 1 | OK_{LV | LED | LED_THT:LED_D5.0mm | Light emitting diode
D2, | 1 | FAULT_{BMS | LED | LED_THT:LED_D5.0mm | Light emitting diode
D3, | 1 | OK_{AUX | LED | LED_THT:LED_D5.0mm | Light emitting diode
D4, | 1 | OK_{BMS | LED | LED_THT:LED_D5.0mm | Light emitting diode
D5, | 1 | FAULT_{IMD | LED | LED_THT:LED_D5.0mm | Light emitting diode
D6, | 1 | OK_{IMD | LED | LED_THT:LED_D5.0mm | Light emitting diode
D7, | 1 | FAULT_{BSPD | LED | LED_THT:LED_D5.0mm | Light emitting diode
D8, | 1 | OK_{BSPD | LED | LED_THT:LED_D5.0mm | Light emitting diode
D9, | 1 | BSPD_GATE | LED | LED_THT:LED_D5.0mm | Light emitting diode
D10, | 1 | OK_{HV | LED | LED_THT:LED_D5.0mm | Light emitting diode
D11, | 1 | LED0 | LED | LED_THT:LED_D5.0mm | Light emitting diode
D12, | 1 | LED1 | LED | LED_THT:LED_D5.0mm | Light emitting diode
D13, | 1 | LED2 | LED | LED_THT:LED_D5.0mm | Light emitting diode
D14, | 1 | LED3 | LED | LED_THT:LED_D5.0mm | Light emitting diode
D15, | 1 | LED4 | LED | LED_THT:LED_D5.0mm | Light emitting diode
D16, | 1 | LED5 | LED | LED_THT:LED_D5.0mm | Light emitting diode
D17, | 1 | RTD | LED | LED_THT:LED_D5.0mm | Light emitting diode
F1, | 1 | 8A | Fuse | Fuse:Fuseholder_Cylinder-5x20mm_Stelvio-Kontek_PTF78_Horizontal_Open | Fuse
J1, J2, | 2 | 5267-12AX | Conn_01x12_Female | Connector_PinHeader_2.54mm:PinHeader_1x12_P2.54mm_Vertical | Generic connector, single row, 01x12, script generated (kicad-library-utils/schlib/autogen/connector/)
J3, | 1 | 5267-08AX | Conn_01x08_Female | footprint:5566-08 | Generic connector, single row, 01x08, script generated (kicad-library-utils/schlib/autogen/connector/)
J4, | 1 | HIGH_CURRENT | Conn_01x08_Female | footprint:5566-08 | Generic connector, single row, 01x08, script generated (kicad-library-utils/schlib/autogen/connector/)
J5, | 1 | 5267-16AX | Conn_01x16_Female | Connector_PinHeader_2.54mm:PinHeader_1x16_P2.54mm_Vertical | Generic connector, single row, 01x16, script generated (kicad-library-utils/schlib/autogen/connector/)
J6, | 1 | Conn_01x02_Female | Conn_01x02_Female | footprint:5566-02A | Generic connector, single row, 01x02, script generated (kicad-library-utils/schlib/autogen/connector/)
J7, | 1 | 5267-06AX | Conn_01x06_Female | Connector_PinHeader_2.54mm:PinHeader_1x06_P2.54mm_Vertical | Generic connector, single row, 01x06, script generated (kicad-library-utils/schlib/autogen/connector/)
J9, J10, | 2 | 5267-10AX | Conn_01x10_Female | Connector_PinHeader_2.54mm:PinHeader_1x10_P2.54mm_Vertical | Generic connector, single row, 01x10, script generated (kicad-library-utils/schlib/autogen/connector/)
J11, | 1 | Conn_01x06_Male | Conn_01x06_Male | Connector_PinHeader_2.54mm:PinHeader_1x06_P2.54mm_Vertical | Generic connector, single row, 01x06, script generated (kicad-library-utils/schlib/autogen/connector/)
J12, | 1 | Conn_01x01_Male | Conn_01x01_Male | Connector_PinSocket_2.54mm:PinSocket_1x01_P2.54mm_Vertical | Generic connector, single row, 01x01, script generated (kicad-library-utils/schlib/autogen/connector/)
K1, K2, K3, K4, K5, | 5 | HR702NH-DC12V | DIPxx-1Cxx-51x | footprint:HR702 | Standex Meder DIP reed relay, SPDT
K6, | 1 | HR90L2_12V | EC2-3TNU_1 | footprint:HR90L2 | General purpose signal relay, Kemet EC2 Series, DPDT (2 Form C), double coil latching, through hole, 60W/125VA, 220VDC/250VAC, 2A, 3V DC coil
OUTSIDE1, | 1 | 5267-16AX | Conn_01x16_Female | Connector_PinHeader_2.54mm:PinHeader_1x16_P2.54mm_Vertical | Generic connector, single row, 01x16, script generated (kicad-library-utils/schlib/autogen/connector/)
Q1, Q2, Q4, | 3 | IRF640 | IRF740 | footprint:IRF640NPBF | 10A Id, 400V Vds, N-Channel Power MOSFET, 500mOhm Rds, TO-220AB
Q3, | 1 | IRF9540N | IRF9540N | Package_TO_SOT_THT:TO-220-3_Vertical | -23A Id, -100V Vds, 117mOhm Rds, P-Channel HEXFET Power MOSFET, TO-220
Q5, Q6, Q7, Q8, Q9, Q10, Q11, Q12, Q13, Q14, | 10 | 2N3904 | 2N3904 | Package_TO_SOT_THT:TO-92_Inline_Wide | 0.2A Ic, 40V Vce, Small Signal NPN Transistor, TO-92
R1, R4, R10, R11, R13, R14, R15, R16, R19, R25, R33, R34, R35, R36, R48, R49, R55, | 17 | 1k | R_US | Resistor_THT:R_Axial_DIN0207_L6.3mm_D2.5mm_P10.16mm_Horizontal | Resistor, US symbol
R2, R3, R12, R20, R21, R24, R26, R27, R28, R29, R30, R31, R32, R37, R44, R45, R47, R51, | 18 | 10k | R_US | Resistor_THT:R_Axial_DIN0207_L6.3mm_D2.5mm_P10.16mm_Horizontal | Resistor, US symbol
R5, R6, R7, R8, R38, R39, R40, R41, R42, R43, | 10 | 100 | R_US | Resistor_THT:R_Axial_DIN0207_L6.3mm_D2.5mm_P10.16mm_Horizontal | Resistor, US symbol
R9, | 1 | 240K | R_US | Resistor_THT:R_Axial_DIN0207_L6.3mm_D2.5mm_P10.16mm_Horizontal | Resistor, US symbol
R17, | 1 | 200k | R_US | Resistor_THT:R_Axial_DIN0207_L6.3mm_D2.5mm_P10.16mm_Horizontal | Resistor, US symbol
R18, | 1 | 51k | R_US | Resistor_THT:R_Axial_DIN0207_L6.3mm_D2.5mm_P10.16mm_Horizontal | Resistor, US symbol
R22, R23, | 2 | 4M | R_US | Resistor_THT:R_Axial_DIN0207_L6.3mm_D2.5mm_P10.16mm_Horizontal | Resistor, US symbol
R46, | 1 | 3.3k | R_US | Resistor_THT:R_Axial_DIN0207_L6.3mm_D2.5mm_P10.16mm_Horizontal | Resistor, US symbol
R50, | 1 | 4.7k | R_US | Resistor_THT:R_Axial_DIN0207_L6.3mm_D2.5mm_P10.16mm_Horizontal | Resistor, US symbol
R52, R53, R54, R56, R57, R58, | 6 | 2.7k | R_US | Resistor_THT:R_Axial_DIN0207_L6.3mm_D2.5mm_P10.16mm_Horizontal | Resistor, US symbol
RLY1, | 1 | RLY_{BMS | RT424F12_2 | footprint:RT424F12
RLY2, | 1 | RLY_{IMD | RT424F12 | footprint:RT424F12
RLY3, | 1 | RLY_{BSPD | RT424F12 | footprint:RT424F12
RV1, | 1 | TUNE_{BRAKE | R_Potentiometer_US | Potentiometer_THT:Potentiometer_Bourns_3296W_Vertical | Potentiometer, US symbol
RV2, | 1 | TUNE_{HALL | R_Potentiometer_US | Potentiometer_THT:Potentiometer_Bourns_3296W_Vertical | Potentiometer, US symbol
SW2, | 1 | ESP_{RST | SW_Push | footprint:TACT_SWITCH | Push button switch, generic, two pins
SW3, | 1 | CAN_{BMS | SW_DPST_1 | footprint:TOGGLE_SWITCH | Double Pole Single Throw (DPST) Switch
SW4, | 1 | CAN_{INV | SW_DPST_1 | footprint:TOGGLE_SWITCH | Double Pole Single Throw (DPST) Switch
SW5, | 1 | CAN_{LOGGER | SW_DPST_1 | footprint:TOGGLE_SWITCH | Double Pole Single Throw (DPST) Switch
SW6, | 1 | CAN_{ECU | SW_DPST_1 | footprint:TOGGLE_SWITCH | Double Pole Single Throw (DPST) Switch
SW7, | 1 | CAN_{DEBUG | SW_DPST_1 | footprint:TOGGLE_SWITCH | Double Pole Single Throw (DPST) Switch
SW8, | 1 | ESP_{PROGRAM | SW_Push | footprint:TACT_SWITCH | Push button switch, generic, two pins
SW9, | 1 | PROGRAM | SW_Push | footprint:TACT_SWITCH | Push button switch, generic, two pins
U1, | 1 | NE555D | NE555D | footprint:NE555P | Precision Timers, 555 compatible, SOIC-8
U2, U3, | 2 | LM311 | LM311 | footprint:LM311P | Voltage Comparator, DIP-8/SOIC-8
U5, | 1 | 5V Converter | DC-DC_Converter | footprint:DCDC_MODULE
U6, | 1 | 3.3V Converter | DC-DC_Converter | footprint:DCDC_MODULE
U7, | 1 | CAN_TRANSCEIVER | CAN_TRANSCEIVER | footprint:CAN_TRANSIVER
U8, | 1 | D302 | D302 | footprint:SPK_D302
U9, | 1 | ADXL345 | ADXL345 | footprint:ADXL345
U10, | 1 | NEO-7M | NEO-7M | footprint:GPSV3-NE0
U11, | 1 | ESP32-WROOM-32D | ESP32-WROOM-32D | footprint:MODULE_ESP32-WROOM-32D
U12, | 1 | DFR0299 | DFR0299 | footprint:DFR0299 | DFRobot Accessories DFPlayer
U13, U14, | 2 | LM555xN | LM555xN | footprint:NE555P | Timer, 555 compatible, PDIP-8
U15, | 1 | STM32F407VETx | STM32F407VETx | footprint:STM32F407_HOLDER | ARM Cortex-M4 MCU, 512KB flash, 128KB RAM, 168MHz, 1.8-3.6V, 82 GPIO, LQFP-100

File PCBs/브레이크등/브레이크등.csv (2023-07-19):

Source: | G:\Shared drives\A-FA E-포뮬러 전기시스템\회로 및 PCB\PCBs\브레이크등\브레이크등.kicad_sch
Date: | 2023-07-09 오후 8:36:11
Tool: | Eeschema (6.0.8)
Generator: | C:\Program Files\KiCad\6.0\bin\scripting\plugins/bom_csv_grouped_by_value_with_fp.py
Component Count: | 57
Ref | Qnty | Value | Cmp name | Footprint | Description | Vendor
D1, D2, D3, D4, D5, D6, D7, D8, D9, D10, D11, D12, D13, D14, D15, D16, D17, D18, D19, D20, D21, D22, D23, D24, D25, D26, D27, D28, D29, D30, D31, D32, D33, D34, D35, D36, D37, D38, D39, D40, D41, D42, D43, D44, D45, D46, D47, D48, | 48 | LED | LED | LED_SMD:LED_RGB_5050-6_copy | Light emitting diode
J1, | 1 | Conn_01x02_FeMale | Conn_01x02_Female | Connector_Molex:Molex_Mini-Fit_Jr_5569-02A1_2x01_P4.20mm_Horizontal | Generic connector, single row, 01x02, script generated (kicad-library-utils/schlib/autogen/connector/)
R1, R2, R3, R4, R5, R6, R7, R8, | 8 | 30 | R | Resistor_THT:R_Axial_DIN0207_L6.3mm_D2.5mm_P10.16mm_Horizontal | Resistor

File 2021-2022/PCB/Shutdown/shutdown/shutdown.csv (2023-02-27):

Source: | G:\공유 드라이브\A-FA E-포뮬러 전기시스템\PCB\Shutdown\shutdown\shutdown.kicad_sch
Date: | 2022-06-29 오후 7:49:52
Tool: | Eeschema (6.0.2)
Generator: | C:\Program Files\KiCad\6.0\bin\scripting\plugins/bom_csv_grouped_by_value.py
Component Count: | 21
Individual Components:
Item | Qty | Reference(s) | Value | LibPart | Footprint | Datasheet
 |  | D1 | 1N4002 | Diode:1N4001 | Library:1N4002 | http://www.vishay.com/docs/88503/1n4001.pdf
 |  | D2 | 1N4002 | Diode:1N4001 | Library:1N4002 | http://www.vishay.com/docs/88503/1n4001.pdf
 |  | D3 | 1N4002 | Diode:1N4001 | Library:1N4002 | http://www.vishay.com/docs/88503/1n4001.pdf
 |  | D4 | 1N4002 | Diode:1N4001 | Library:1N4002 | http://www.vishay.com/docs/88503/1n4001.pdf
 |  | J1 | HV_AUX1 | Connector:Conn_01x02_Female | Connector_Molex:Molex_SPOX_5267-02A_1x02_P2.50mm_Vertical | ~
 |  | J2 | HV_AUX2 | Connector:Conn_01x02_Female | Connector_Molex:Molex_SPOX_5267-02A_1x02_P2.50mm_Vertical | ~
 |  | J3 | HV_AUX3 | Connector:Conn_01x02_Female | Connector_Molex:Molex_SPOX_5267-02A_1x02_P2.50mm_Vertical | ~
 |  | J4 | BOTS | Connector:Conn_01x02_Female | Connector_Molex:Molex_SPOX_5267-02A_1x02_P2.50mm_Vertical | ~
 |  | J5 | LVMS | Connector:Conn_01x02_Female | Connector_Molex:Molex_SPOX_5267-02A_1x02_P2.50mm_Vertical | ~
 |  | J6 | Conn_01x06_Female | Connector:Conn_01x06_Female | Connector_Molex:Molex_SPOX_5267-06A_1x06_P2.50mm_Vertical | ~
 |  | J7 | Conn_01x04_Female | Connector:Conn_01x04_Female | Connector_Molex:Molex_SPOX_5267-04A_1x04_P2.50mm_Vertical | ~
 |  | J8 | Conn_01x06_Female | Connector:Conn_01x06_Female | Connector_Molex:Molex_SPOX_5267-06A_1x06_P2.50mm_Vertical | ~
 |  | J9 | HVMS | Connector:Conn_01x02_Female | Connector_Molex:Molex_SPOX_5267-02A_1x02_P2.50mm_Vertical | ~
 |  | J10 | Conn_01x06_Female | Connector:Conn_01x06_Female | Connector_Molex:Molex_SPOX_5267-06A_1x06_P2.50mm_Vertical | ~
 |  | J11 | Conn_01x02_Female | Connector:Conn_01x02_Female | Connector_Molex:Molex_SPOX_5267-02A_1x02_P2.50mm_Vertical | ~
 |  | JP1 | HVD_INTERLOCK | Device:Jumper | Connector_Molex:Molex_SPOX_5267-02A_1x02_P2.50mm_Vertical
 |  | RELAY_AIR+_ACTIVE1 | JQ1-12V-F | Relay:DIPxx-1Axx-12x | Relay_THT:Relay_StandexMeder_DIP_LowProfile | https://standexelectronics.com/wp-content/uploads/datasheet_reed_relay_DIP.pdf
 |  | RELAY_BMS1 | ADJ14012 | NewThing:ADJ14024 | Library:ADJ14012
 |  | RELAY_BSPD1 | ADJ14012 | NewThing:ADJ14024 | Library:ADJ14012
 |  | RELAY_HVD_INTERLOCK1 | JQ1-12V-F | Relay:DIPxx-1Axx-12x | Relay_THT:Relay_StandexMeder_DIP_LowProfile | https://standexelectronics.com/wp-content/uploads/datasheet_reed_relay_DIP.pdf
 |  | RELAY_IMD1 | ADJ14012 | NewThing:ADJ14024 | Library:ADJ14012
Collated Components:
Item | Qty | Reference(s) | Value | LibPart | Footprint | Datasheet
1 | 4 | D1, D2, D3, D4 | 1N4002 | Diode:1N4001 | Library:1N4002 | http://www.vishay.com/docs/88503/1n4001.pdf
2 | 1 | J1 | HV_AUX1 | Connector:Conn_01x02_Female | Connector_Molex:Molex_SPOX_5267-02A_1x02_P2.50mm_Vertical | ~
3 | 1 | J2 | HV_AUX2 | Connector:Conn_01x02_Female | Connector_Molex:Molex_SPOX_5267-02A_1x02_P2.50mm_Vertical | ~
4 | 1 | J3 | HV_AUX3 | Connector:Conn_01x02_Female | Connector_Molex:Molex_SPOX_5267-02A_1x02_P2.50mm_Vertical | ~
5 | 1 | J4 | BOTS | Connector:Conn_01x02_Female | Connector_Molex:Molex_SPOX_5267-02A_1x02_P2.50mm_Vertical | ~
6 | 1 | J5 | LVMS | Connector:Conn_01x02_Female | Connector_Molex:Molex_SPOX_5267-02A_1x02_P2.50mm_Vertical | ~
7 | 3 | J6, J8, J10 | Conn_01x06_Female | Connector:Conn_01x06_Female | Connector_Molex:Molex_SPOX_5267-06A_1x06_P2.50mm_Vertical | ~
8 | 1 | J7 | Conn_01x04_Female | Connector:Conn_01x04_Female | Connector_Molex:Molex_SPOX_5267-04A_1x04_P2.50mm_Vertical | ~
9 | 1 | J9 | HVMS | Connector:Conn_01x02_Female | Connector_Molex:Molex_SPOX_5267-02A_1x02_P2.50mm_Vertical | ~
10 | 1 | J11 | Conn_01x02_Female | Connector:Conn_01x02_Female | Connector_Molex:Molex_SPOX_5267-02A_1x02_P2.50mm_Vertical | ~
11 | 1 | JP1 | HVD_INTERLOCK | Device:Jumper | Connector_Molex:Molex_SPOX_5267-02A_1x02_P2.50mm_Vertical
12 | 2 | RELAY_AIR+_ACTIVE1, RELAY_HVD_INTERLOCK1 | JQ1-12V-F | Relay:DIPxx-1Axx-12x | Relay_THT:Relay_StandexMeder_DIP_LowProfile | https://standexelectronics.com/wp-content/uploads/datasheet_reed_relay_DIP.pdf
13 | 3 | RELAY_BMS1, RELAY_BSPD1, RELAY_IMD1 | ADJ14012 | NewThing:ADJ14024 | Library:ADJ14012

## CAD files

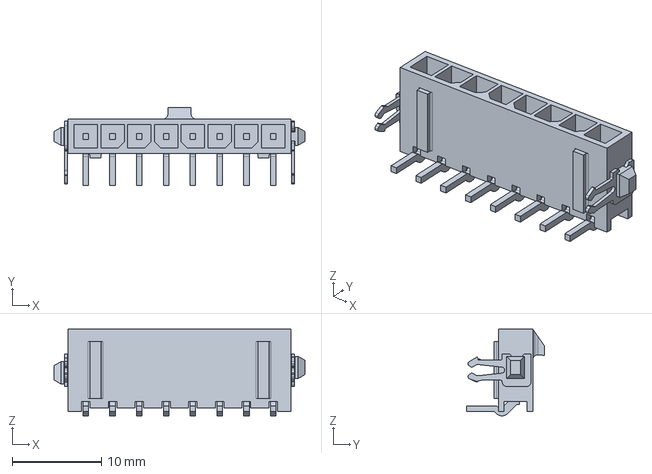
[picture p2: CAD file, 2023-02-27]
2021-2022/Schematics/PARTS/2-1445088-8/2-1445088-8.step
28.1 x 8.72 x 9.73 mm

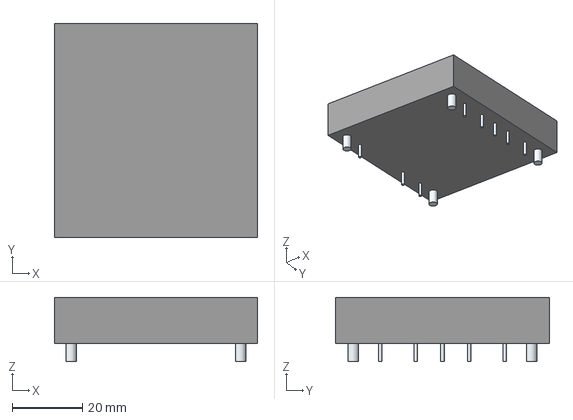
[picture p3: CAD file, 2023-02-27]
symbols/QHL300300S28/3D/QHL300300S28.stp
57.9 x 61.0 x 18.3 mm
Leads

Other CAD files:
symbols/QHL300300S28/Allegro/qhl300300s28.psm
symbols/QHL300300S28/DEHDL/qhl300300s28/chips/chips.prt

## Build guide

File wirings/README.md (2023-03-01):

# 전기시스템 배선 및 커넥터 규격

## 요구사항
Python 3.7 이상

## 설치
[Graphviz](https://graphviz.org/download/) 설치

```shell
pip install wireviz
```

## 실행
`run.bat` 실행 또는
```shell
wireviz wire.yml -o output/wire
```

## 결과물
`output/wire.png`

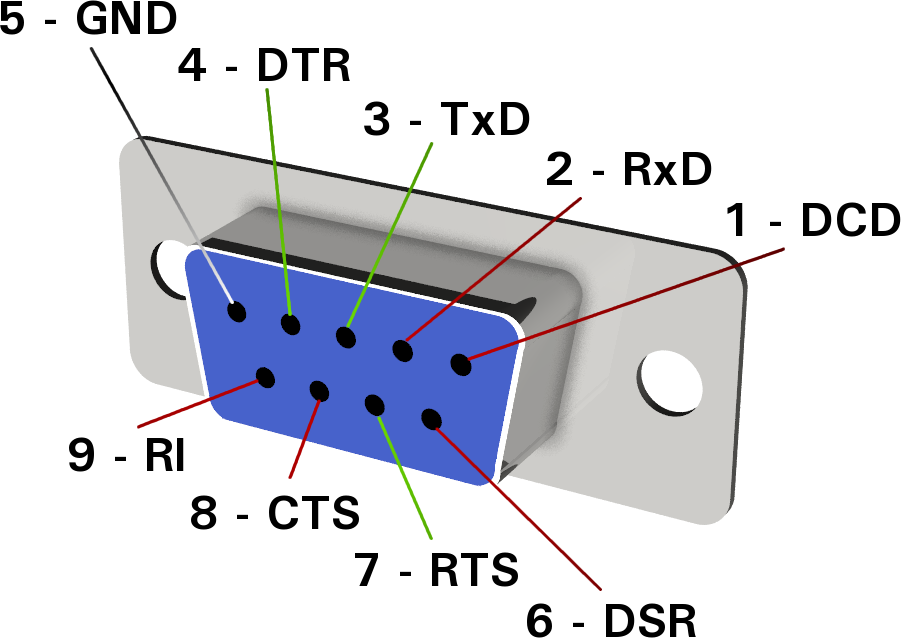
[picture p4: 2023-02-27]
wirings/image/rs232.png

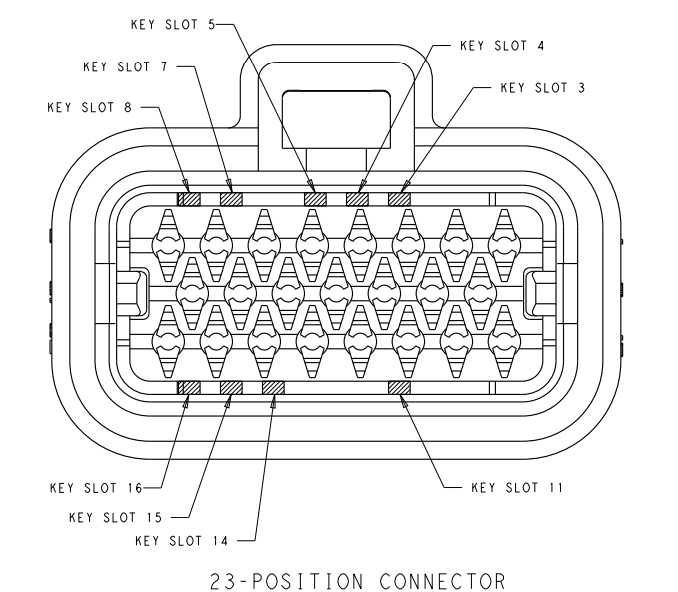
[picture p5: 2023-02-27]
wirings/image/J2.png

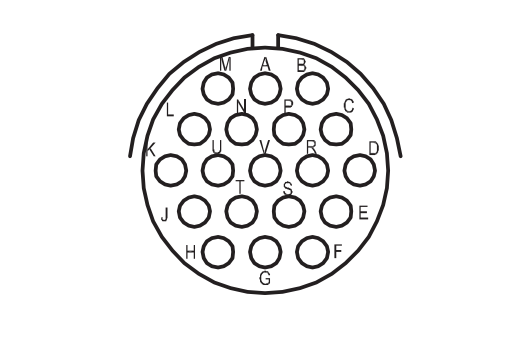
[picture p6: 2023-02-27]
wirings/image/lpt.png

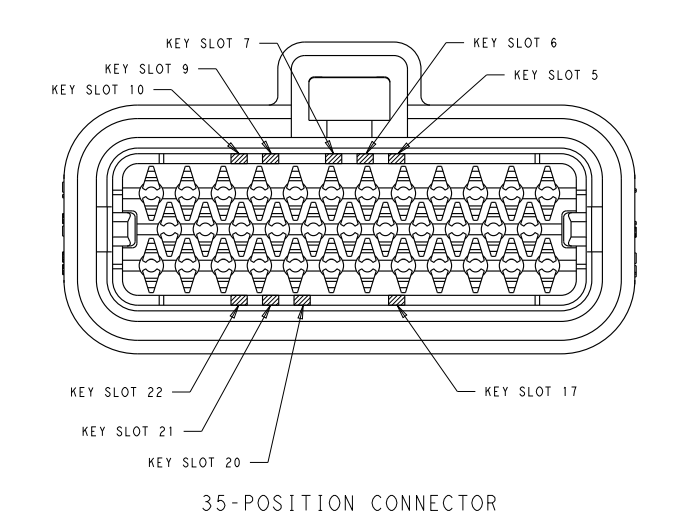
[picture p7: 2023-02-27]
wirings/image/J1.png

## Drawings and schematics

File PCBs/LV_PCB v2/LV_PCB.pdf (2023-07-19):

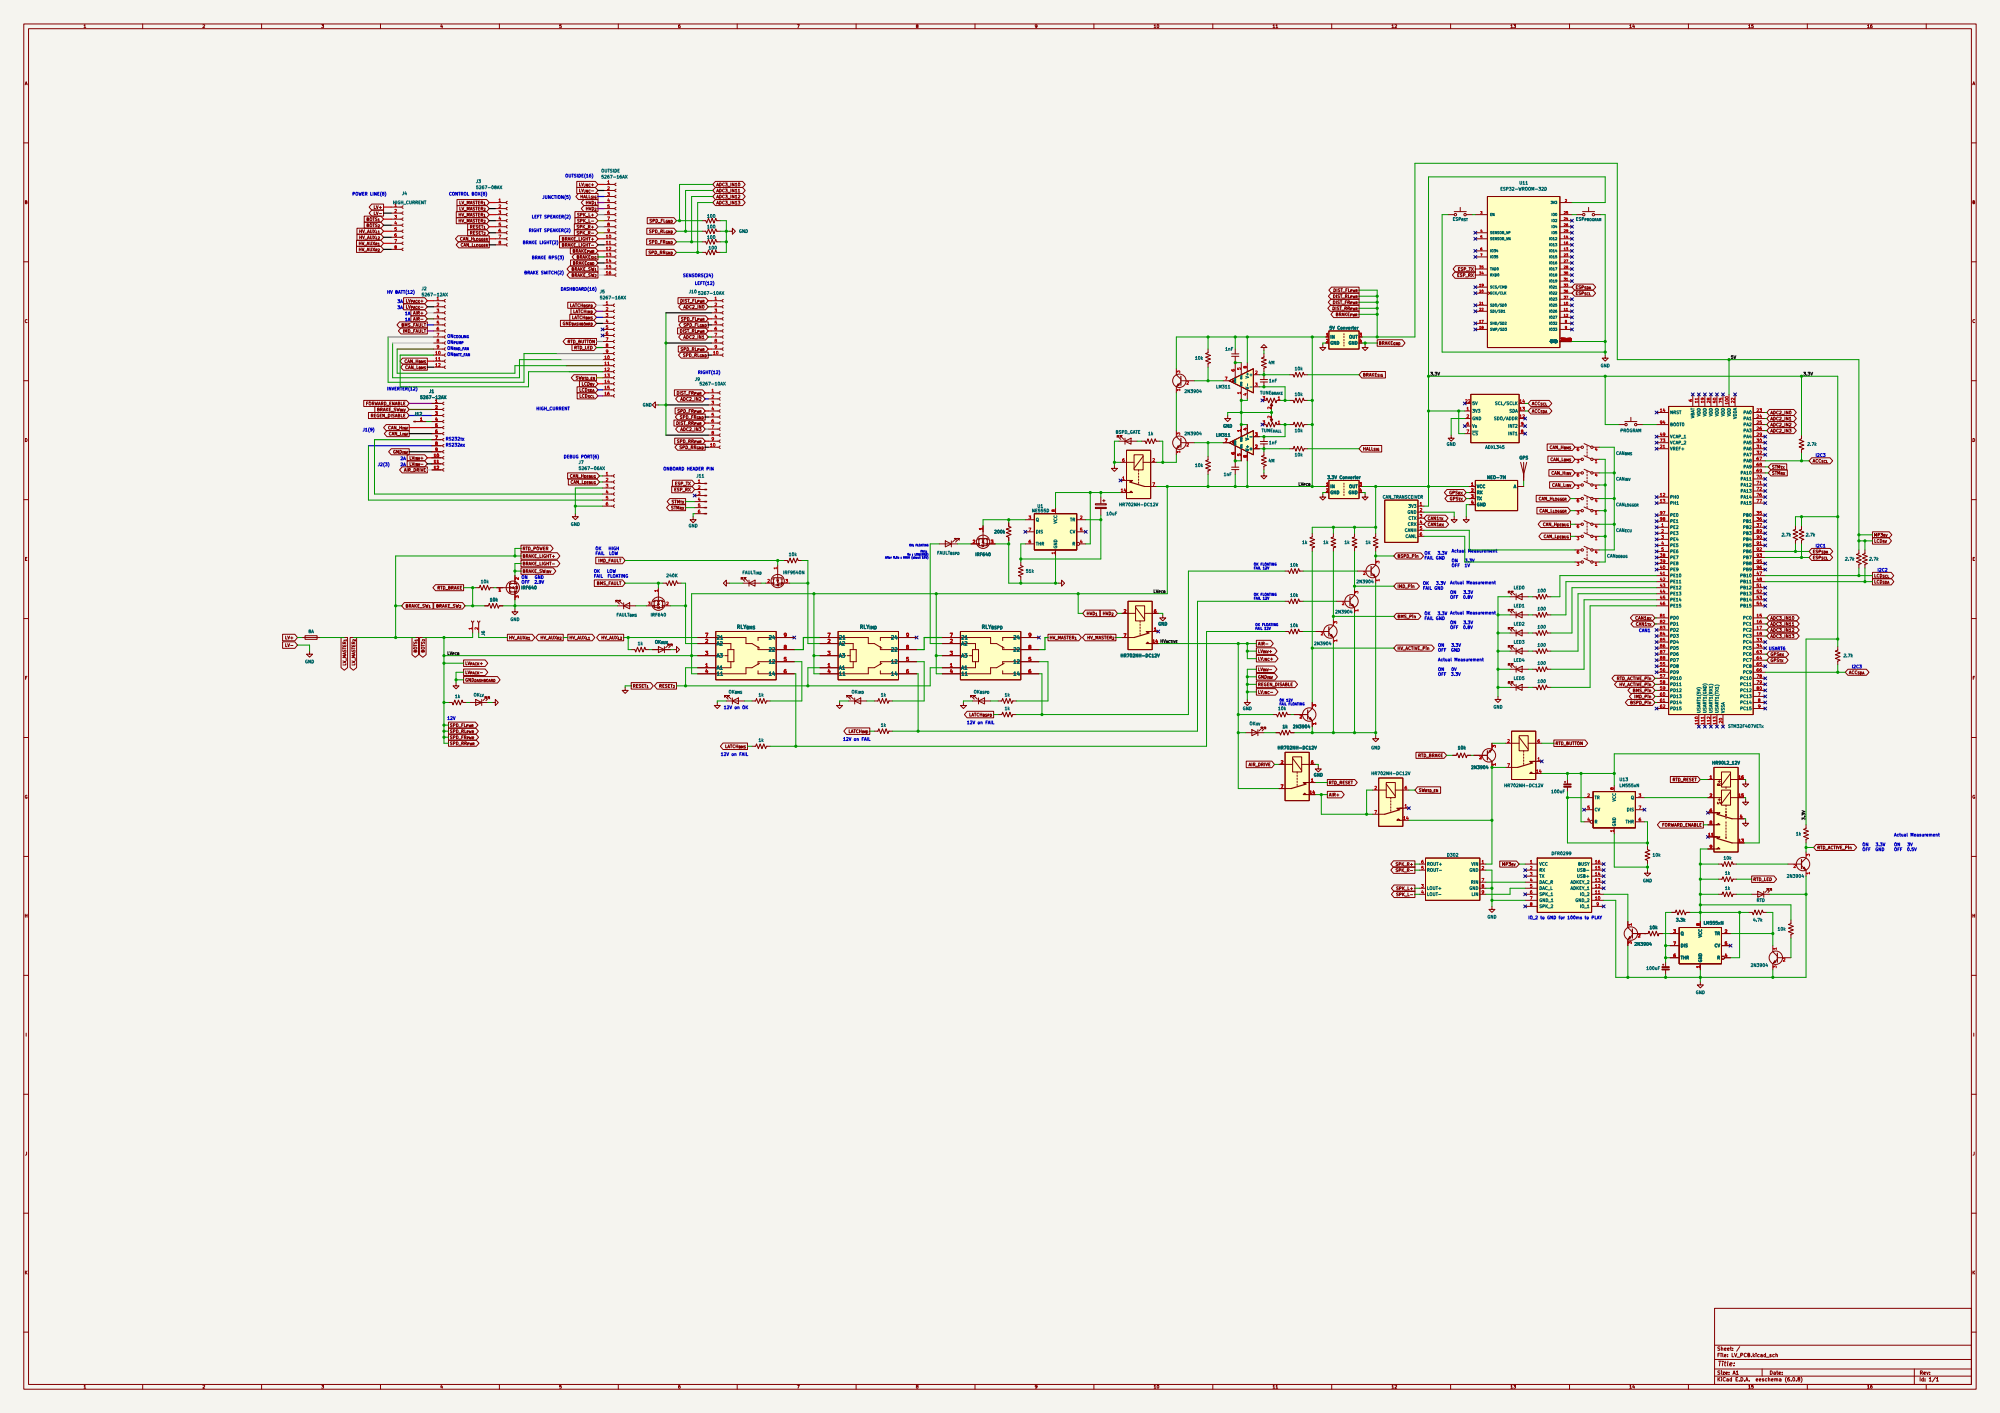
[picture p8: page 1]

FAIL: 0s : LOW(GND) After 0.5s : HIGH (about 10V) 12V on FAIL

Actual Measurement ON 3.3V OFF 1V OK 3.3V
FAIL GND

Actual Measurement ON 3.3V OFF 0.8V

Actual Measurement ON 3.3V OFF 0.8V OK 3.3V

IO_2 to GND for 100ms to PLAY

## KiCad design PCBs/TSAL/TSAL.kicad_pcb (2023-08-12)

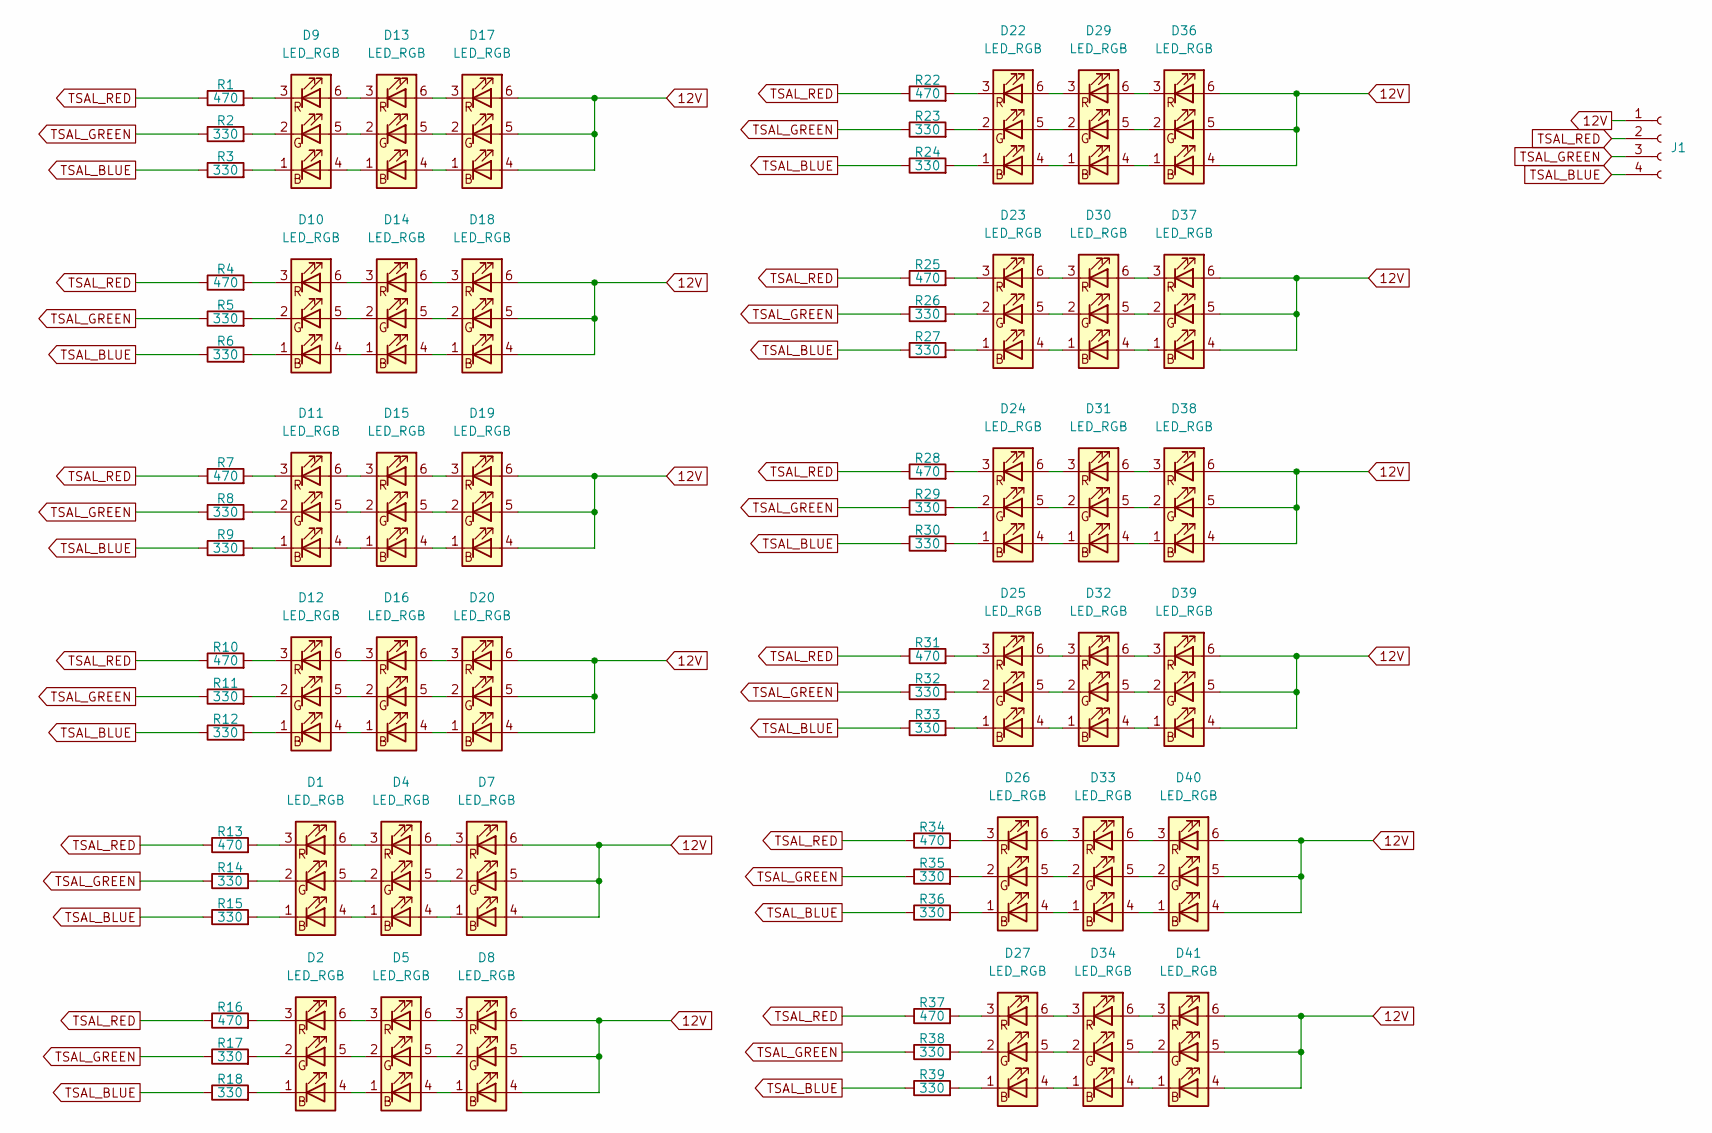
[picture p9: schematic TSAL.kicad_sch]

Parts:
D1, D2, D4, D5, D7, D8, D9, D10, D11, D12, D13, D14, D15, D16, D17, D18, D19, D20, D22, D23, D24, D25, D26, D27, D29, D30, D31, D32, D33, D34, D36, D37, D38, D39, D40, D41: LED_RGB; LED_RGB_5050-6
J1: Conn_01x04_Female; PinHeader_1x04_P2.54mm_Vertical
R1, R4, R7, R10, R13, R16, R22, R25, R28, R31, R34, R37: 470; R_1206_3216Metric_Pad1.30x1.75mm_HandSolder
R2, R3, R5, R6, R8, R9, R11, R12, R14, R15, R17, R18, R23, R24, R26, R27, R29, R30, R32, R33, R35, R36, R38, R39: 330; R_1206_3216Metric_Pad1.30x1.75mm_HandSolder

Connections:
12V: D7.4 (BA), D7.5 (GA), D7.6 (RA), D8.4 (BA), D8.5 (GA), D8.6 (RA), D17.4 (BA), D17.5 (GA), D17.6 (RA), D18.4 (BA), D18.5 (GA), D18.6 (RA), D19.4 (BA), D19.5 (GA), D19.6 (RA), D20.4 (BA), D20.5 (GA), D20.6 (RA), D36.4 (BA), D36.5 (GA), D36.6 (RA), D37.4 (BA), D37.5 (GA), D37.6 (RA), D38.4 (BA), D38.5 (GA), D38.6 (RA), D39.4 (BA), D39.5 (GA), D39.6 (RA), D40.4 (BA), D40.5 (GA), D40.6 (RA), D41.4 (BA), D41.5 (GA), D41.6 (RA), J1.1
unnamed: D1.1 (BK), R15.2
unnamed: D1.2 (GK), R14.2
unnamed: D1.3 (RK), R13.2
unnamed: D1.4 (BA), D4.1 (BK)
unnamed: D1.5 (GA), D4.2 (GK)
unnamed: D1.6 (RA), D4.3 (RK)
unnamed: D2.1 (BK), R18.2
unnamed: D2.2 (GK), R17.2
unnamed: D2.3 (RK), R16.2
unnamed: D2.4 (BA), D5.1 (BK)
unnamed: D2.5 (GA), D5.2 (GK)
unnamed: D2.6 (RA), D5.3 (RK)
unnamed: D4.4 (BA), D7.1 (BK)
unnamed: D4.5 (GA), D7.2 (GK)
unnamed: D4.6 (RA), D7.3 (RK)
unnamed: D5.4 (BA), D8.1 (BK)
unnamed: D5.5 (GA), D8.2 (GK)
unnamed: D5.6 (RA), D8.3 (RK)
unnamed: D9.1 (BK), R3.2
unnamed: D9.2 (GK), R2.2
unnamed: D9.3 (RK), R1.2
unnamed: D10.1 (BK), R6.2
unnamed: D10.2 (GK), R5.2
unnamed: D10.3 (RK), R4.2
unnamed: D10.4 (BA), D14.1 (BK)
unnamed: D10.5 (GA), D14.2 (GK)
unnamed: D10.6 (RA), D14.3 (RK)
unnamed: D11.1 (BK), R9.2
unnamed: D11.2 (GK), R8.2
unnamed: D11.3 (RK), R7.2
unnamed: D11.4 (BA), D15.1 (BK)
unnamed: D11.5 (GA), D15.2 (GK)
unnamed: D11.6 (RA), D15.3 (RK)
unnamed: D12.1 (BK), R12.2
unnamed: D12.2 (GK), R11.2
unnamed: D12.3 (RK), R10.2
unnamed: D12.4 (BA), D16.1 (BK)
unnamed: D12.5 (GA), D16.2 (GK)
unnamed: D12.6 (RA), D16.3 (RK)
unnamed: D9.4 (BA), D13.1 (BK)
unnamed: D9.5 (GA), D13.2 (GK)
unnamed: D9.6 (RA), D13.3 (RK)
unnamed: D13.4 (BA), D17.1 (BK)
unnamed: D13.5 (GA), D17.2 (GK)
unnamed: D13.6 (RA), D17.3 (RK)
unnamed: D14.4 (BA), D18.1 (BK)
unnamed: D14.5 (GA), D18.2 (GK)
unnamed: D14.6 (RA), D18.3 (RK)
unnamed: D15.4 (BA), D19.1 (BK)
unnamed: D15.5 (GA), D19.2 (GK)
unnamed: D15.6 (RA), D19.3 (RK)
unnamed: D16.4 (BA), D20.1 (BK)
unnamed: D16.5 (GA), D20.2 (GK)
unnamed: D16.6 (RA), D20.3 (RK)
unnamed: D22.1 (BK), R24.2
unnamed: D22.2 (GK), R23.2
unnamed: D22.3 (RK), R22.2
unnamed: D22.4 (BA), D29.1 (BK)
unnamed: D22.5 (GA), D29.2 (GK)
unnamed: D22.6 (RA), D29.3 (RK)
unnamed: D23.1 (BK), R27.2
unnamed: D23.2 (GK), R26.2
unnamed: D23.3 (RK), R25.2
unnamed: D23.4 (BA), D30.1 (BK)
unnamed: D23.5 (GA), D30.2 (GK)
unnamed: D23.6 (RA), D30.3 (RK)
unnamed: D24.1 (BK), R30.2
unnamed: D24.2 (GK), R29.2
unnamed: D24.3 (RK), R28.2
unnamed: D24.4 (BA), D31.1 (BK)
unnamed: D24.5 (GA), D31.2 (GK)
unnamed: D24.6 (RA), D31.3 (RK)
unnamed: D25.1 (BK), R33.2
unnamed: D25.2 (GK), R32.2
unnamed: D25.3 (RK), R31.2
unnamed: D25.4 (BA), D32.1 (BK)
unnamed: D25.5 (GA), D32.2 (GK)
unnamed: D25.6 (RA), D32.3 (RK)
unnamed: D26.1 (BK), R36.2
unnamed: D26.2 (GK), R35.2
unnamed: D26.3 (RK), R34.2
unnamed: D26.4 (BA), D33.1 (BK)
unnamed: D26.5 (GA), D33.2 (GK)
unnamed: D26.6 (RA), D33.3 (RK)
unnamed: D27.1 (BK), R39.2
unnamed: D27.2 (GK), R38.2
unnamed: D27.3 (RK), R37.2
unnamed: D27.4 (BA), D34.1 (BK)
unnamed: D27.5 (GA), D34.2 (GK)
unnamed: D27.6 (RA), D34.3 (RK)
unnamed: D29.4 (BA), D36.1 (BK)
unnamed: D29.5 (GA), D36.2 (GK)
unnamed: D29.6 (RA), D36.3 (RK)
unnamed: D30.4 (BA), D37.1 (BK)
unnamed: D30.5 (GA), D37.2 (GK)
unnamed: D30.6 (RA), D37.3 (RK)
unnamed: D31.4 (BA), D38.1 (BK)
unnamed: D31.5 (GA), D38.2 (GK)
unnamed: D31.6 (RA), D38.3 (RK)
unnamed: D32.4 (BA), D39.1 (BK)
unnamed: D32.5 (GA), D39.2 (GK)
unnamed: D32.6 (RA), D39.3 (RK)
unnamed: D33.4 (BA), D40.1 (BK)
unnamed: D33.5 (GA), D40.2 (GK)
unnamed: D33.6 (RA), D40.3 (RK)
unnamed: D34.4 (BA), D41.1 (BK)
unnamed: D34.5 (GA), D41.2 (GK)
unnamed: D34.6 (RA), D41.3 (RK)
TSAL_BLUE: J1.4, R3.1, R6.1, R9.1, R12.1, R15.1, R18.1, R24.1, R27.1, R30.1, R33.1, R36.1, R39.1
TSAL_GREEN: J1.3, R2.1, R5.1, R8.1, R11.1, R14.1, R17.1, R23.1, R26.1, R29.1, R32.1, R35.1, R38.1
TSAL_RED: J1.2, R1.1, R4.1, R7.1, R10.1, R13.1, R16.1, R22.1, R25.1, R28.1, R31.1, R34.1, R37.1

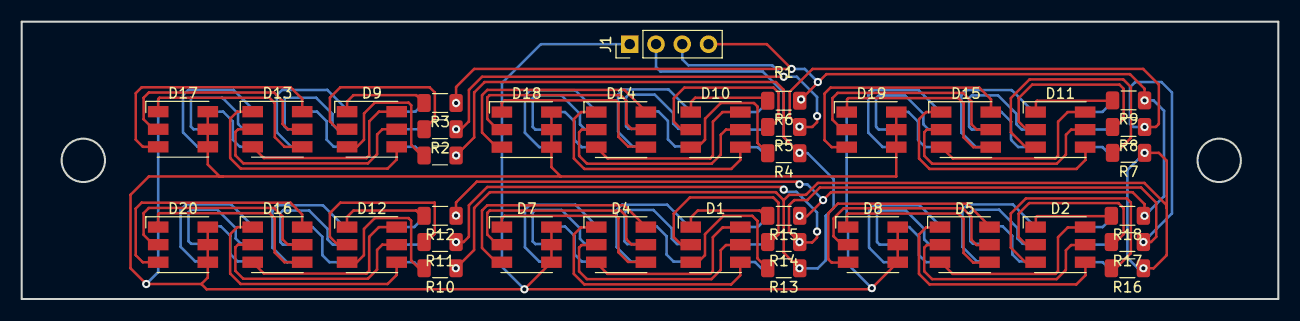
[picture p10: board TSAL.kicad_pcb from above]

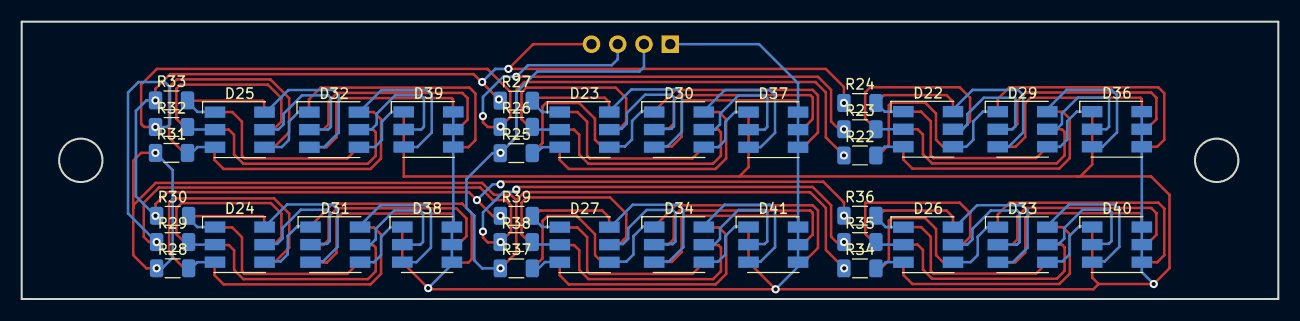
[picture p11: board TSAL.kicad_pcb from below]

Board: 2 copper layers, 121.7 x 26.9 mm, 73 parts (36 on the bottom side), 112 nets.

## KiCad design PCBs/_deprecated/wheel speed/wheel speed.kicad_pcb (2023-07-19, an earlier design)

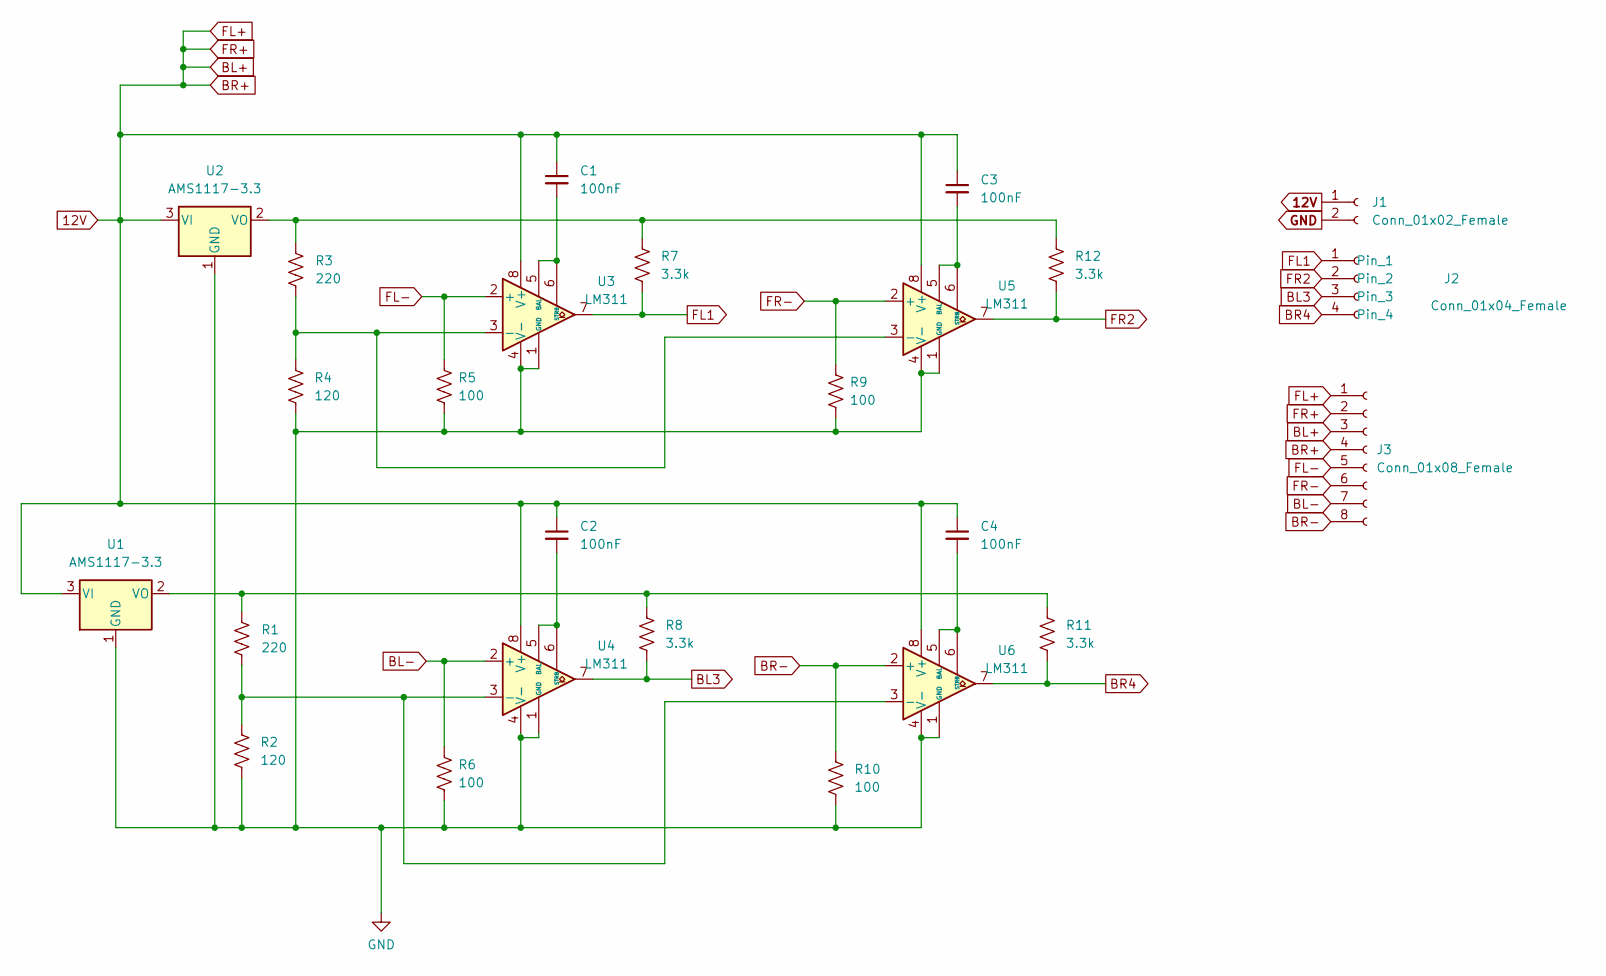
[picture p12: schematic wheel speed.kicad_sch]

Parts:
C1, C2, C3, C4: 100nF; C_Disc_D5.0mm_W2.5mm_P2.50mm
J1: Conn_01x02_Female; PinHeader_1x02_P2.54mm_Vertical
J2: Conn_01x04_Female; PinHeader_1x04_P2.54mm_Vertical
J3: Conn_01x08_Female; PinHeader_1x08_P2.54mm_Vertical
R1, R3: 220; R_Axial_DIN0207_L6.3mm_D2.5mm_P10.16mm_Horizontal
R2, R4: 120; R_Axial_DIN0207_L6.3mm_D2.5mm_P10.16mm_Horizontal
R5, R6, R9, R10: 100; R_Axial_DIN0207_L6.3mm_D2.5mm_P10.16mm_Horizontal
R7, R8, R11, R12: 3.3k; R_Axial_DIN0207_L6.3mm_D2.5mm_P10.16mm_Horizontal
U1, U2: AMS1117-3.3; AMS1117-5.0
U3, U4, U5, U6: LM311; LM311P

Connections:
12V: C1.1, C2.1, C3.1, C4.1, J1.1, J3.1, J3.2, J3.3, J3.4, U1.3 (VI), U2.3 (VI), U3.8 (V+), U4.8 (V+), U5.8 (V+), U6.8 (V+)
BL3: J2.3, R8.1, U4.7
BL-: J3.7, R6.2, U4.2 (+)
BR4: J2.4, R11.1, U6.7
BR-: J3.8, R10.2, U6.2 (+)
FL1: J2.1, R7.1, U3.7
FL-: J3.5, R5.2, U3.2 (+)
FR2: J2.2, R12.1, U5.7
FR-: J3.6, R9.2, U5.2 (+)
GND: J1.2, R2.1, R4.1, R5.1, R6.1, R9.1, R10.1, U1.1 (GND), U2.1 (GND), U3.1 (GND), U3.4 (V-), U4.1 (GND), U4.4 (V-), U5.1 (GND), U5.4 (V-), U6.1 (GND), U6.4 (V-)
unnamed: C1.2, U3.5 (BAL), U3.6 (STRB)
unnamed: C2.2, U4.5 (BAL), U4.6 (STRB)
unnamed: C3.2, U5.5 (BAL), U5.6 (STRB)
unnamed: C4.2, U6.5 (BAL), U6.6 (STRB)
unnamed: R1.1, R8.2, R11.2, U1.2 (VO)
unnamed: R1.2, R2.2, U4.3 (-), U6.3 (-)
unnamed: R3.2, R4.2, U3.3 (-), U5.3 (-)
unnamed: R3.1, R7.2, R12.2, U2.2 (VO)

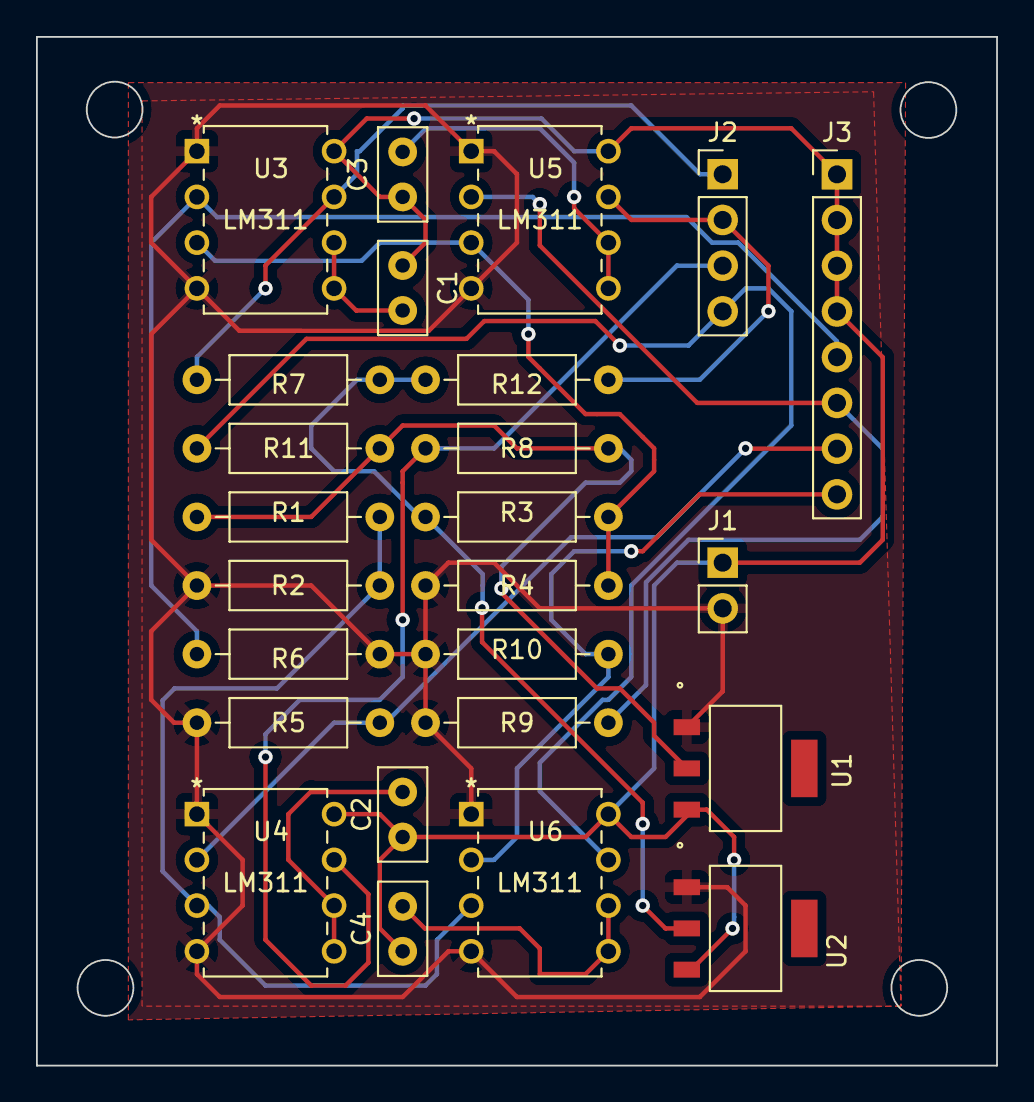
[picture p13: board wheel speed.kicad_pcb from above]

Board: 2 copper layers, 53.3 x 57.1 mm, 25 parts (0 on the bottom side), 18 nets.

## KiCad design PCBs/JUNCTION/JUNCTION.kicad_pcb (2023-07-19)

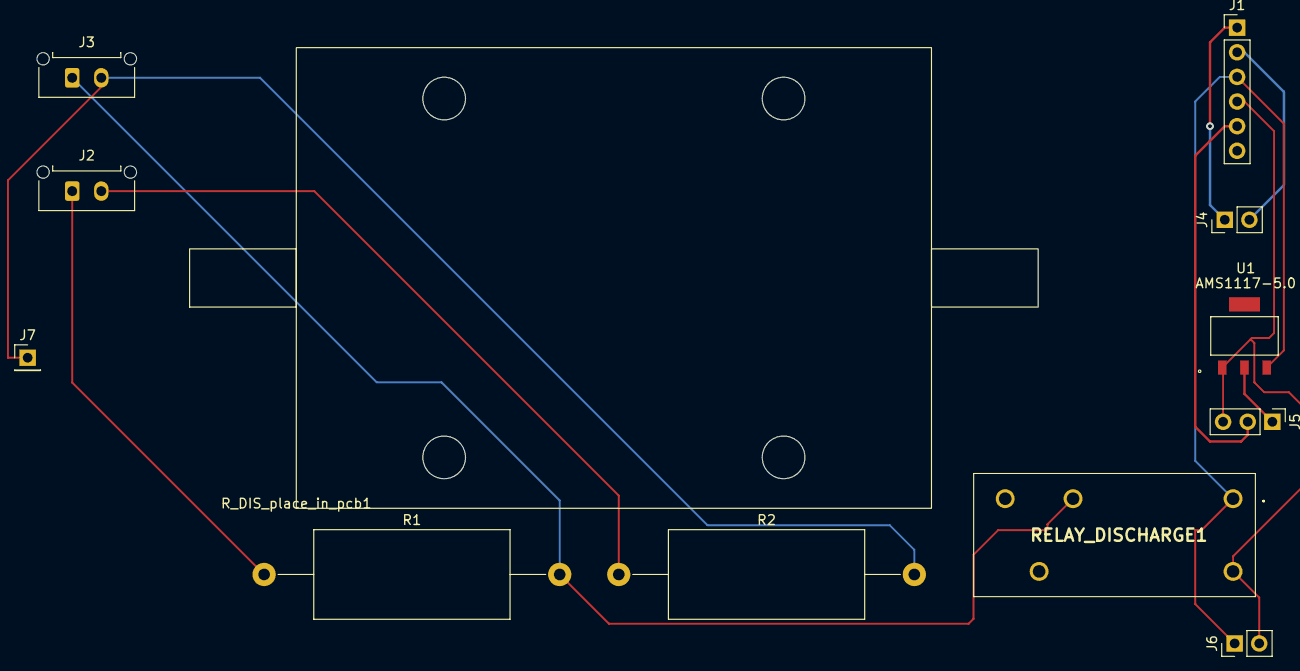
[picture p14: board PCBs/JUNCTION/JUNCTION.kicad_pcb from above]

Board: 2 copper layers, 12 parts (0 on the bottom side), 10 nets.

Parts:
J1: JUNC; PinHeader_1x06_P2.54mm_Vertical
J2: TSMP; Molex_Micro-Fit_3.0_43650-0215_1x02_P3.00mm_Vertical
J3: HV; Molex_Micro-Fit_3.0_43650-0215_1x02_P3.00mm_Vertical
J4: HVD_IN; PinHeader_1x02_P2.54mm_Vertical
J5: HALL; PinHeader_1x03_P2.54mm_Vertical
J6: ENERGYMETER; PinHeader_1x02_P2.54mm_Vertical
J7: R_DISCHARGE; PinHeader_1x01_P2.54mm_Vertical
R1, R2: 10k; R_Axial_DIN0922_L20.0mm_D9.0mm_P30.48mm_Horizontal
RELAY_DISCHARGE1: G2RL-1_12DC; G2RL112DC
R_DIS_place_in_pcb1: 1k; HSC100
U1: AMS1117-5.0

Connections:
5V_{HALL}: J5.1, U1.2 (VO)
HALL_SIG: J1.5, J5.2
HV+: J3.1, R1.2, RELAY_DISCHARGE1.2 (NC)
HV-: J3.2, J7.1, R2.2
HVD1: J1.1, J4.1
HVD2: J1.2, J4.2
LV_{JNC}+: J1.3, J6.1, RELAY_DISCHARGE1.1 (COIL_1), U1.3 (VI)
LV_{JNC}-: J1.4, J5.3, J6.2, RELAY_DISCHARGE1.5 (COIL_2), U1.1 (GND)
TSMP+: J2.1, R1.1
TSMP-: J2.2, R2.1

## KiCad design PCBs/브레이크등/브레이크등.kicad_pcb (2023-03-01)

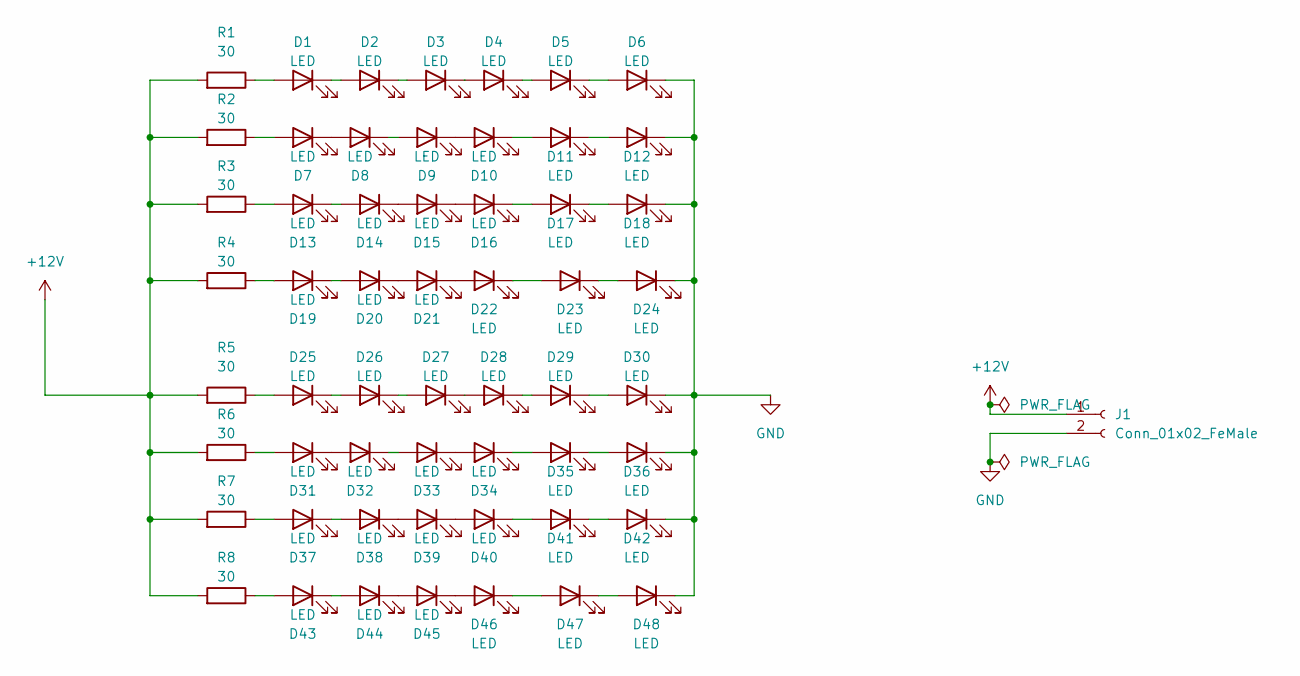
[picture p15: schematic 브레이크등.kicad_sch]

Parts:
D1, D2, D3, D4, D5, D6, D7, D8, D9, D10, D11, D12, D13, D14, D15, D16, D17, D18, D19, D20, D21, D22, D23, D24, D25, D26, D27, D28, D29, D30, D31, D32, D33, D34, D35, D36, D37, D38, D39, D40, D41, D42, D43, D44, D45, D46, D47, D48: LED; LED_RGB_5050-6_copy
J1: Conn_01x02_FeMale; Molex_Mini-Fit_Jr_5569-02A1_2x01_P4.20mm_Horizontal
R1, R2, R3, R4, R5, R6, R7, R8: 30; R_Axial_DIN0207_L6.3mm_D2.5mm_P10.16mm_Horizontal

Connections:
+12V: J1.1, R1.2, R2.2, R3.2, R4.2, R5.2, R6.2, R7.2, R8.2
GND: D6.1 (K), D12.1 (K), D18.1 (K), D24.1 (K), D30.1 (K), D36.1 (K), D42.1 (K), D48.1 (K), J1.2
unnamed: D1.1 (K), D2.2 (A)
unnamed: D1.2 (A), R1.1
unnamed: D2.1 (K), D3.2 (A)
unnamed: D3.1 (K), D4.2 (A)
unnamed: D4.1 (K), D5.2 (A)
unnamed: D5.1 (K), D6.2 (A)
unnamed: D7.1 (K), D8.2 (A)
unnamed: D7.2 (A), R2.1
unnamed: D8.1 (K), D9.2 (A)
unnamed: D10.1 (K), D11.2 (A)
unnamed: D9.1 (K), D10.2 (A)
unnamed: D11.1 (K), D12.2 (A)
unnamed: D13.1 (K), D14.2 (A)
unnamed: D13.2 (A), R3.1
unnamed: D14.1 (K), D15.2 (A)
unnamed: D15.1 (K), D16.2 (A)
unnamed: D16.1 (K), D17.2 (A)
unnamed: D17.1 (K), D18.2 (A)
unnamed: D19.1 (K), D20.2 (A)
unnamed: D19.2 (A), R4.1
unnamed: D20.1 (K), D21.2 (A)
unnamed: D21.1 (K), D22.2 (A)
unnamed: D22.1 (K), D23.2 (A)
unnamed: D23.1 (K), D24.2 (A)
unnamed: D25.1 (K), D26.2 (A)
unnamed: D25.2 (A), R5.1
unnamed: D26.1 (K), D27.2 (A)
unnamed: D27.1 (K), D28.2 (A)
unnamed: D28.1 (K), D29.2 (A)
unnamed: D29.1 (K), D30.2 (A)
unnamed: D31.1 (K), D32.2 (A)
unnamed: D31.2 (A), R6.1
unnamed: D32.1 (K), D33.2 (A)
unnamed: D33.1 (K), D34.2 (A)
unnamed: D34.1 (K), D35.2 (A)
unnamed: D35.1 (K), D36.2 (A)
unnamed: D37.1 (K), D38.2 (A)
unnamed: D37.2 (A), R7.1
unnamed: D38.1 (K), D39.2 (A)
unnamed: D39.1 (K), D40.2 (A)
unnamed: D40.1 (K), D41.2 (A)
unnamed: D41.1 (K), D42.2 (A)
unnamed: D43.1 (K), D44.2 (A)
unnamed: D43.2 (A), R8.1
unnamed: D44.1 (K), D45.2 (A)
unnamed: D45.1 (K), D46.2 (A)
unnamed: D46.1 (K), D47.2 (A)
unnamed: D47.1 (K), D48.2 (A)

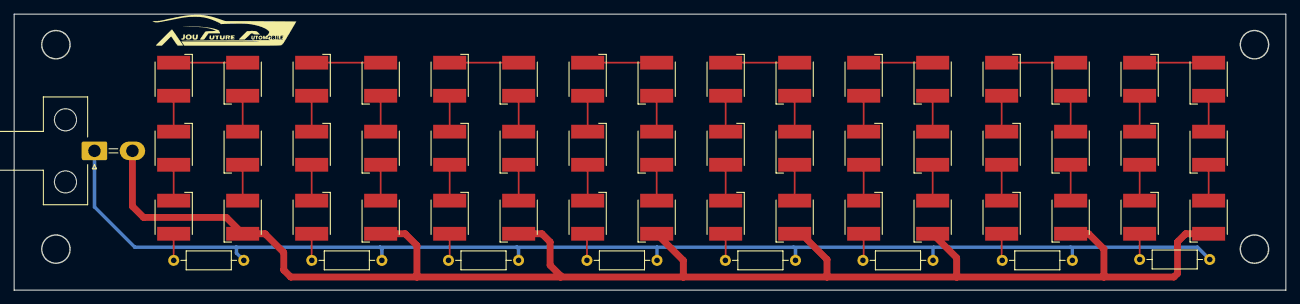
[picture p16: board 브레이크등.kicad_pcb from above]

Board: 2 copper layers, 184.3 x 40.0 mm, 58 parts (0 on the bottom side), 50 nets.

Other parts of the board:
A-FA: bf078263-bd62-418a-b936-95124366838e

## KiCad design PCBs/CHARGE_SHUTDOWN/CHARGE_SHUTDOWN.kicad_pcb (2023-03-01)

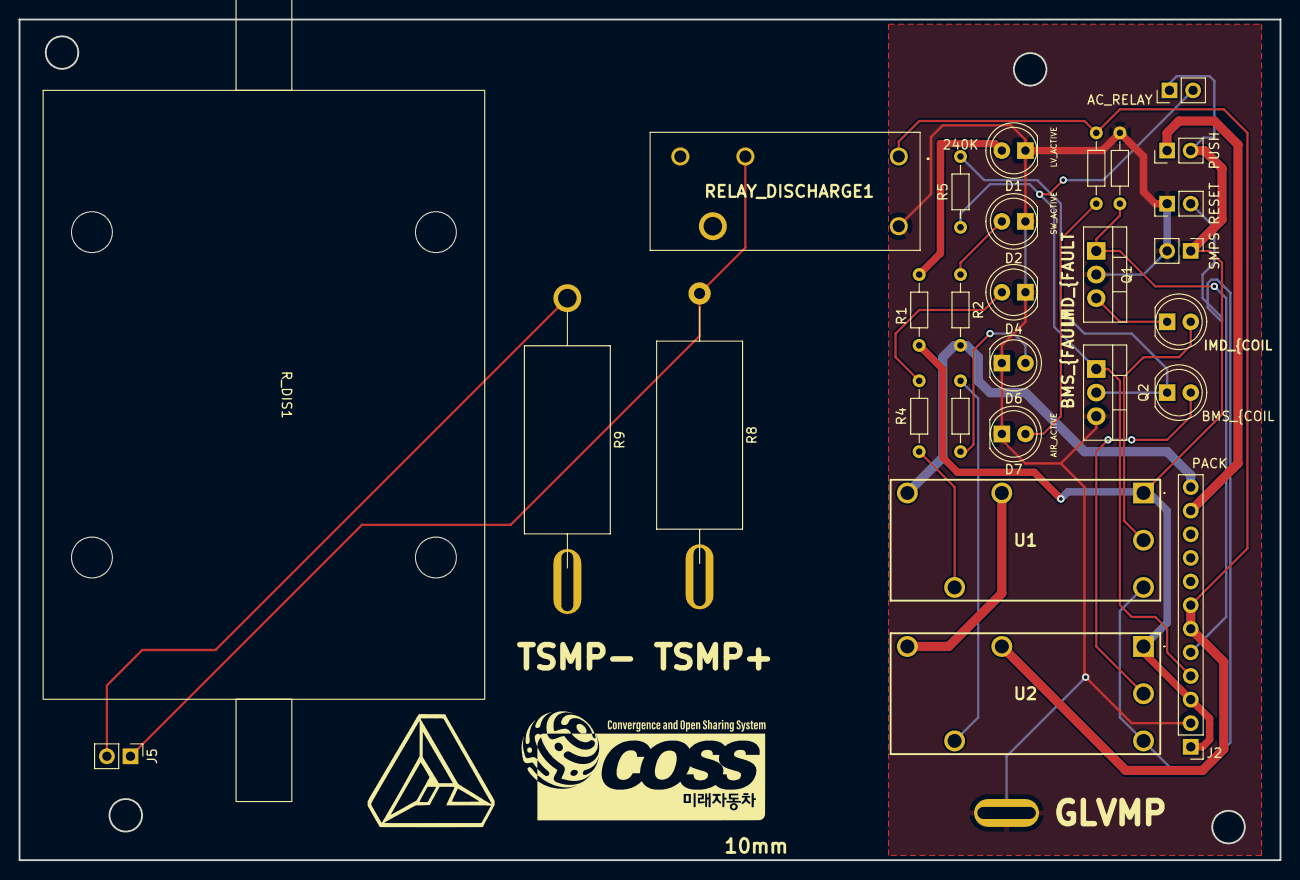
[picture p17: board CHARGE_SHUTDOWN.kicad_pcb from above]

Board: 2 copper layers, 135.6 x 90.4 mm, 29 parts (0 on the bottom side), 22 nets.

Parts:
AC_RELAY: AC_RELAY; PinHeader_1x02_P2.54mm_Vertical
D1: LV_ACTIVE; LED_D5.0mm
D2: SW_ACTIVE; LED_D5.0mm
D3: IMD_{COIL; LED_D5.0mm
D4: IMD_{FAULT; LED_D5.0mm
D5: BMS_{COIL; LED_D5.0mm
D6: BMS_{FAULT; LED_D5.0mm
D7: AIR_ACTIVE; LED_D5.0mm
J2: PACK; PinHeader_1x12_P2.54mm_Vertical
J5: HV; PinHeader_1x02_P2.54mm_Vertical
J7: Conn_01x01_Female; Banana_Jack_1Pin
PUSH: PUSH_ROTATE; PinHeader_1x02_P2.54mm_Vertical
Q1: IRF9540N; TO-220-3_Vertical
Q2: IRF740; TO-220-3_Vertical
R1, R2, R3, R4, R6, R7: 10k; R_Axial_DIN0204_L3.6mm_D1.6mm_P7.62mm_Horizontal
R5: 240K; R_Axial_DIN0204_L3.6mm_D1.6mm_P7.62mm_Horizontal
R8, R9: 10K; R_Axial_DIN0922_L20.0mm_D9.0mm_P30.48mm_Horizontal
RELAY_DISCHARGE1: G2RL-1_12DC; G2RL112DC
RESET: RESET; PinHeader_1x02_P2.54mm_Vertical
R_DIS1: 1k; HSC100
SMPS: SMPS; PinHeader_1x02_P2.54mm_Vertical
U1, U2: ADJ14012; ADJ14024

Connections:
AIR+_ACTIVE: J2.6, J2.7, R7.2, RELAY_DISCHARGE1.1 (COIL_1), U2.2 (Out)
CHARGER_SAFETY: AC_RELAY.2, J2.4, Q2.1 (G), R5.1
CHARGE_POWER: AC_RELAY.1, J2.1, J2.3, PUSH.2, R1.2, SMPS.1, U1.1 (V), U2.1 (V)
GND_BOX: D1.1 (K), D2.1 (K), D4.1 (K), D6.1 (K), D7.1 (K), J2.2, J7.1, Q1.2 (D), Q2.3 (S), R3.1, RELAY_DISCHARGE1.5 (COIL_2), RESET.1, SMPS.2
IMD_FAULT: J2.5, Q1.1 (G), R3.2
INTERLOCK_{1}: J2.11, PUSH.1
INTERLOCK_{2}: J2.12, R2.2, U1.4 (12V)
unnamed: D1.2 (A), R1.1
unnamed: D2.2 (A), R2.1
unnamed: D3.1 (K), Q1.3 (S)
unnamed: D3.2 (A), U1.9 (D)
unnamed: D4.2 (A), R4.2
unnamed: D5.1 (K), Q2.2 (D), R5.2
unnamed: D5.2 (A), U2.9 (D)
unnamed: D6.2 (A), R6.2
unnamed: D7.2 (A), R7.1
unnamed: J5.1, R8.1, RELAY_DISCHARGE1.2 (NC)
unnamed: J5.2, R9.1
unnamed: R4.1, U1.6 (N)
unnamed: R6.1, U2.6 (N)
unnamed: U1.2 (Out), U2.4 (12V)
Reset_Button: RESET.2, U1.8 (L), U2.8 (L)

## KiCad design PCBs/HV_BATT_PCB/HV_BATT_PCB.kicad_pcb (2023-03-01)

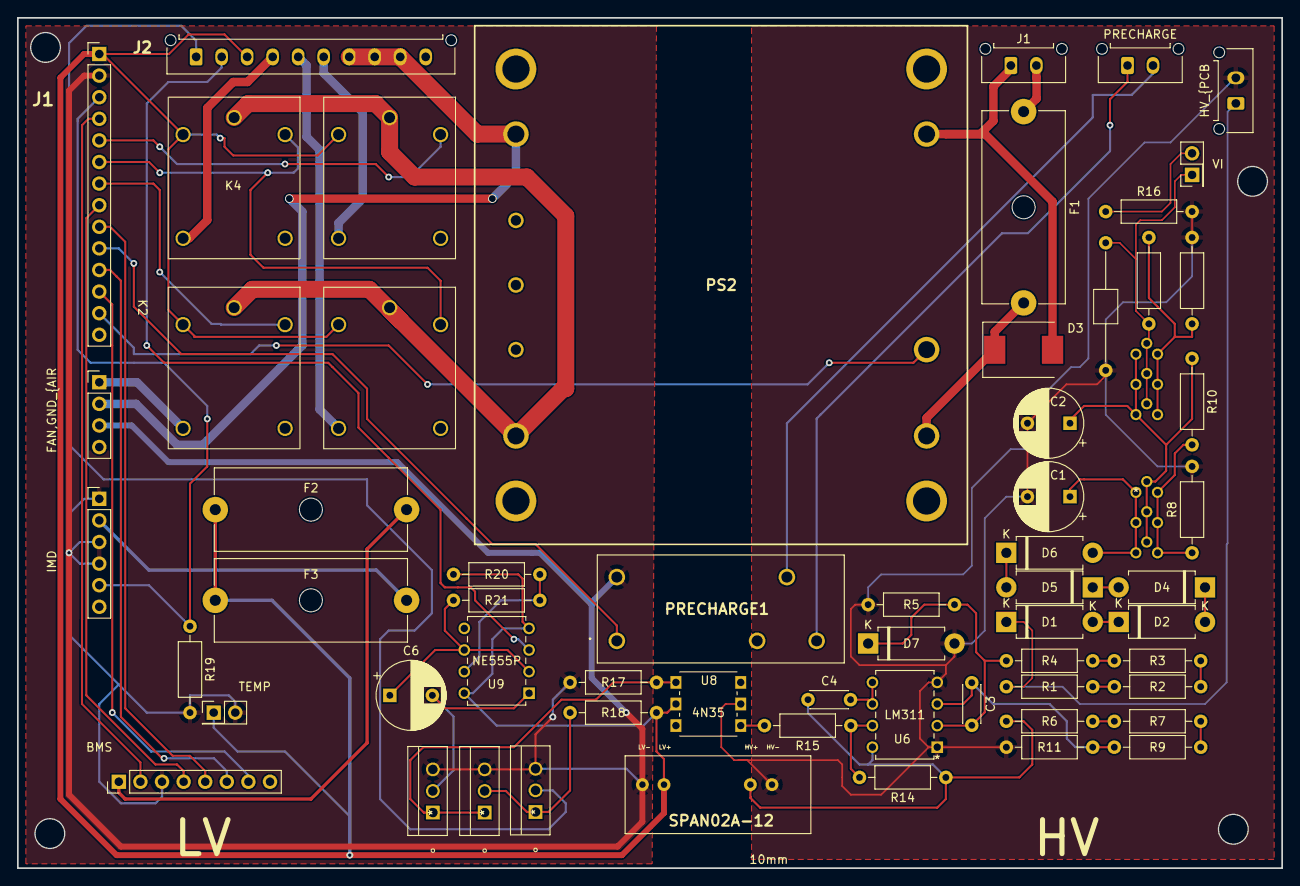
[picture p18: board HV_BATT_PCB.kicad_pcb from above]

Board: 2 copper layers, 148.7 x 100.0 mm, 66 parts (0 on the bottom side), 56 nets.

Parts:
BMS: Conn_01x08_Male; PinHeader_1x08_P2.54mm_Vertical
C1, C2: 2.2uF; CP_Radial_D8.0mm_P5.00mm
C3: 1nF; C_Disc_D4.3mm_W1.9mm_P5.00mm
C4: 1uF; C_Disc_D4.3mm_W1.9mm_P5.00mm
C5: 1uF; C_Axial_L3.8mm_D2.6mm_P15.00mm_Horizontal
C6: 1uF; CP_Radial_D8.0mm_P5.00mm
D1, D2, D4, D5, D6, D7: 1N5349; D_DO-15_P10.16mm_Horizontal
D3: TVS; D_SMC
F1: SMCJ440A; Fuseholder_Cylinder-5x20mm_Schurter_0031_8201_Horizontal_Op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
F2: 1A Fuse; Fuseholder_Cylinder-5x20mm_Schurter_0031_8201_Horizontal_Op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
F3: 3A Fuse; Fuseholder_Cylinder-5x20mm_Schurter_0031_8201_Horizontal_Op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
FAN,GND_{AIR: Conn_01x04_Male; PinHeader_1x04_P2.54mm_Vertical
HV_{PCB: HV_{PCB; Molex_Micro-Fit_3.0_43650-0215_1x02_P3.00mm_Vertical
IMD: Conn_01x06_Male; PinHeader_1x06_P2.54mm_Vertical
J1: Conn_01x02_Male; Molex_Micro-Fit_3.0_43650-0215_1x02_P3.00mm_Vertical
J1#2: Conn_01x14_Male; PinHeader_1x14_P2.54mm_Vertical
J2: Conn_01x10_Male; Molex_Micro-Fit_3.0_43650-1015_1x10_P3.00mm_Vertical
K1: PUMP; HR702
K2: FAN_R; HR702
K3: FAN_L; HR702
K4: LV_BATT_FAN; HR702
PRECHARGE: Conn_01x02_Male; Molex_Micro-Fit_3.0_43650-0215_1x02_P3.00mm_Vertical
PRECHARGE1: G2RL-1_12DC; G2RL112DC
PS1: SPAN02A-12; SPAN02A12
PS2: QHL300300S12; QHL300300S28
Q1, Q2, Q3: IRF640; IRF640NPBF
R1, R2, R3, R4, R6, R7, R9, R11: 4.7M; R_Axial_DIN0207_L6.3mm_D2.5mm_P10.16mm_Horizontal
R5: 1M; R_Axial_DIN0207_L6.3mm_D2.5mm_P10.16mm_Horizontal
R8: 390k; R_Axial_DIN0207_L6.3mm_D2.5mm_P10.16mm_Horizontal
R10: 4.7k; R_Axial_DIN0207_L6.3mm_D2.5mm_P10.16mm_Horizontal
R12: 18k; R_Axial_DIN0207_L6.3mm_D2.5mm_P10.16mm_Horizontal
R13: 12k; R_Axial_DIN0207_L6.3mm_D2.5mm_P10.16mm_Horizontal
R14, R18: 10k; R_Axial_DIN0207_L6.3mm_D2.5mm_P10.16mm_Horizontal
R15, R19: 2k2; R_Axial_DIN0207_L6.3mm_D2.5mm_P10.16mm_Horizontal
R16: 1k; R_Axial_DIN0207_L6.3mm_D2.5mm_P10.16mm_Horizontal
R17: 100k; R_Axial_DIN0207_L6.3mm_D2.5mm_P10.16mm_Horizontal
R20, R21: 240k; R_Axial_DIN0207_L6.3mm_D2.5mm_P10.16mm_Horizontal
TEMP: Conn_01x02_Male; PinHeader_2x01_P2.54mm_Vertical
U1, U2, U3, U4, U5, U7: LR8; LR8N3-G
U6: LM311; LM311P
U8: 4N35
U9: NE555P
VI1: Conn_01x02_Male; PinHeader_2x01_P2.54mm_Vertical

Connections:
BMS_FAULT: BMS.2, J1#2.4
CAN_H_{BMS: BMS.4, J1#2.8
CAN_L_{BMS: BMS.5, J1#2.9
CHARGER_SAFETY: BMS.7, J1#2.12
CHARGE_POWER: BMS.6, J1#2.11
GND_AIR: BMS.3, FAN,GND_{AIR.3, IMD.1, IMD.3, IMD.4, J1#2.2, PRECHARGE1.5 (COIL_2), PS1.1 (-VIN), Q1.3 (S), Q2.3 (S), Q3.3 (S), R17.1, R19.2, TEMP.2
HV_{PCB}+: D1.1 (K), HV_{PCB.1, R1.1
HV_{PCB}-: C1.2, C2.2, C5.2, D7.2 (A), HV_{PCB.2, PS1.7 (-VOUT), R5.2, R8.2, R11.2, R12.2, R16.2, U6.1 (GND), U6.4 (V-), U8.2
IMD_FAULT: IMD.5, J1#2.3, R19.1
LV_{BATT_FAN}+: FAN,GND_{AIR.1, K2.14
LV_{BATT_FAN}-: FAN,GND_{AIR.2, J2.7, J2.8, J2.9, PS2.4 (-VOUT)
LV_{BMS}+: BMS.1, F2.2
LV_{COOLING1}: K1.7, K2.7, K3.7, K4.7, PS2.8 (+VOUT)
LV_{FAN_L}+: J2.5, K3.14
LV_{FAN_R}+: J2.4, K4.14
LV_{IMD}+: F3.2, IMD.2
LV_{PACK}+: F2.1, F3.1, J1#2.1, J2.3, K1.2, K2.2, K3.2, K4.2, PS1.2 (+VIN), R18.1, R20.2, TEMP.1, U8.5, U9.4 (R), U9.8 (VCC)
LV_{PUMP}+: J2.6, K1.14
unnamed: C1.1, D6.2 (A), U1.1 (IN), U2.1 (IN), U3.1 (IN)
unnamed: C2.1, R10.1, U1.2 (OUT), U2.2 (OUT), U3.2 (OUT), U4.1 (IN), U5.1 (IN), U7.1 (IN)
unnamed: C3.1, R9.2, R11.1, U6.3 (-)
unnamed: C3.2, D7.1 (K), R4.2, R5.1, U6.2 (+)
unnamed: C4.1, PS1.6 (+VOUT), R6.1, R14.1, U6.8 (V+)
unnamed: C4.2, U6.5 (BAL), U6.6 (STRB)
unnamed: C6.1, R21.1, U9.2 (TR), U9.6 (THR)
unnamed: C6.2, Q3.2 (D), U9.1 (GND)
unnamed: D1.2 (A), D2.1 (K)
unnamed: D2.2 (A), D4.1 (K)
unnamed: D3.1 (A1), F1.2, PS2.1 (+VIN)
unnamed: D3.2 (A2), J1.1, PS2.3 (-VIN)
unnamed: D4.2 (A), D5.1 (K)
unnamed: D5.2 (A), D6.1 (K)
unnamed: F1.1, J1.2
unnamed: Q1.1 (G), Q2.2 (D), R18.2
unnamed: Q2.1 (G), Q3.1 (G), R17.2, U8.4
unnamed: R1.2, R2.1
unnamed: R2.2, R3.1
unnamed: R3.2, R4.1
unnamed: R6.2, R7.1
unnamed: R7.2, R9.1
unnamed: R8.1, R10.2, U1.3 (ADJ), U2.3 (ADJ), U3.3 (ADJ)
unnamed: R12.1, R13.2, U4.3 (ADJ), U5.3 (ADJ), U7.3 (ADJ)
unnamed: R14.2, R15.1, U6.7
unnamed: R15.2, U8.1
unnamed: R20.1, R21.2, U9.7 (DIS)
ON_{BATT_FAN}: J1#2.7, K2.6
ON_{COOLING: J1#2.13, PS2.2 (REMOTE_ON/OFF)
ON_{PUMP}: J1#2.5, K1.6
ON_{RAD_FAN}: J1#2.6, K3.6, K4.6
PRECHARGE_DRIVE: J1#2.10, PRECHARGE1.1 (COIL_1)
RELAY_PRECHARGE: PRECHARGE.1, PRECHARGE1.3 (NO)
R_PRECHARGE: PRECHARGE.2, PRECHARGE1.4 (COM)
TSAL_GREEN: J2.1, Q1.2 (D)
TSAL_RED: J2.2, U9.3 (Q)
VI_LED+: C5.1, R13.1, U4.2 (OUT), U5.2 (OUT), U7.2 (OUT), VI1.1
VI_LED-: R16.1, VI1.2

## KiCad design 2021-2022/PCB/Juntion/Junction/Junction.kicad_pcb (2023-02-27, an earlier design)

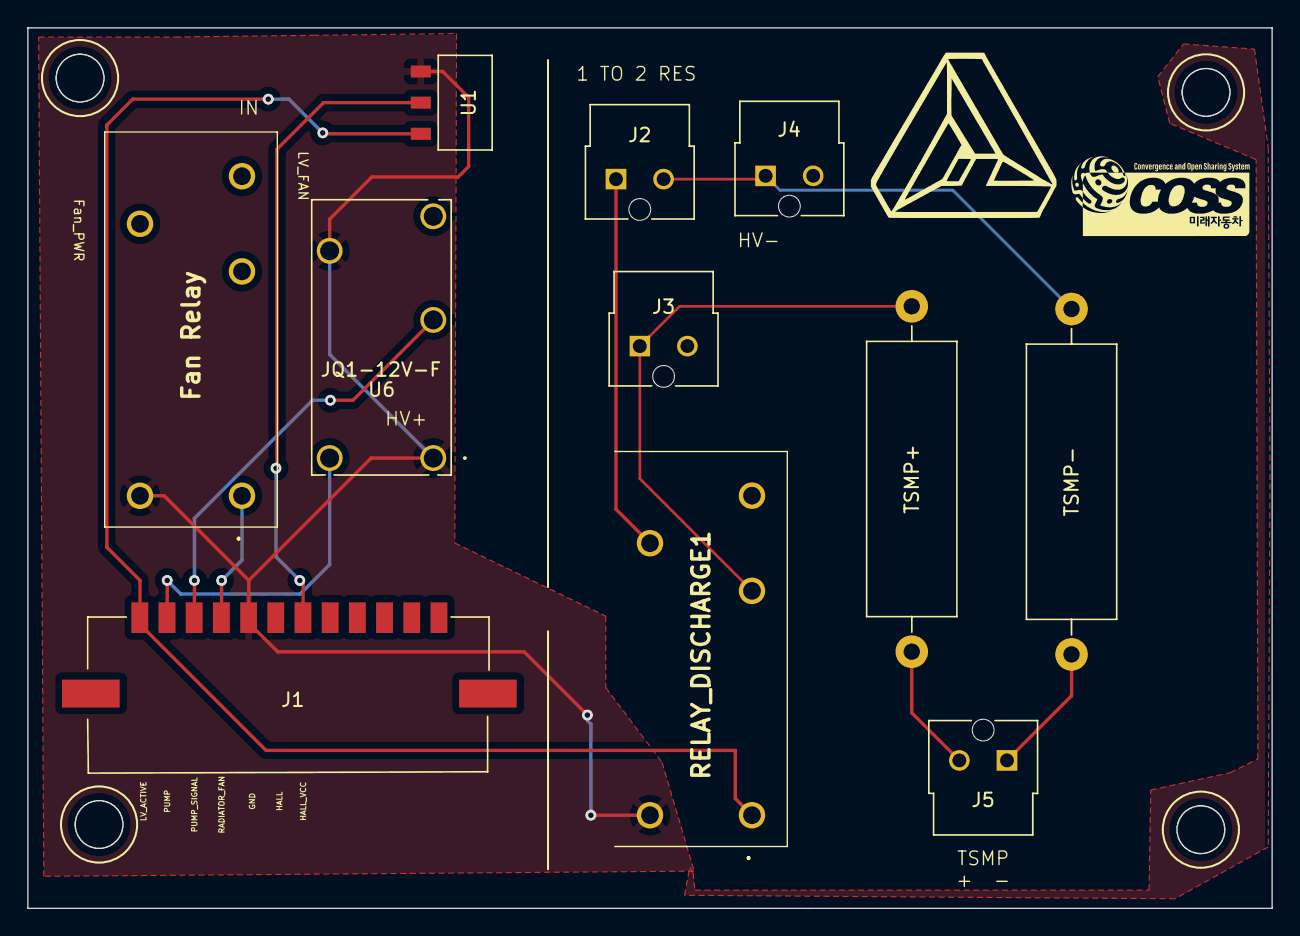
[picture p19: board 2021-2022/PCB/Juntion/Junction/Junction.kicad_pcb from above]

Board: 2 copper layers, 91.5 x 64.8 mm, 11 parts (0 on the bottom side), 11 nets.

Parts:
Fan Relay: G2RL-1_12DC; G2RL112DC
J1: Conn_01x12_Female; 5600201220
J2, J3, J4, J5: Conn_01x02_Female; 1722861102
RELAY_DISCHARGE1: G2RL-1_12DC; G2RL112DC
TSMP+: R_Axial_Power_L20.0mm_W6.4mm_P25.40mm
TSMP-: R_Axial_Power_L20.0mm_W6.4mm_P25.40mm
U1: AMS1117-5.0
U6: JQ1-12V-F

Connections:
++: J5.2, TSMP+.1
--: J5.1, TSMP-.1
GND: Fan Relay.5 (COIL_2), J1.5, RELAY_DISCHARGE1.5 (COIL_2), U1.1 (GND), U6.1, U6.4
HV_IN+: J3.1, RELAY_DISCHARGE1.2 (NC), TSMP+.2
HV_IN-: J2.2, J4.1, TSMP-.2
LV_ACTIVE: J1.1, RELAY_DISCHARGE1.1 (COIL_1), U1.3 (VI)
unnamed: J2.1, RELAY_DISCHARGE1.4 (COM)
PUMP: J1.2, U6.5
PUMP_SIGNAL: J1.3, U6.2
RADIATOR_FAN: Fan Relay.1 (COIL_1), J1.4
chul: J1.7, U1.2 (VO)

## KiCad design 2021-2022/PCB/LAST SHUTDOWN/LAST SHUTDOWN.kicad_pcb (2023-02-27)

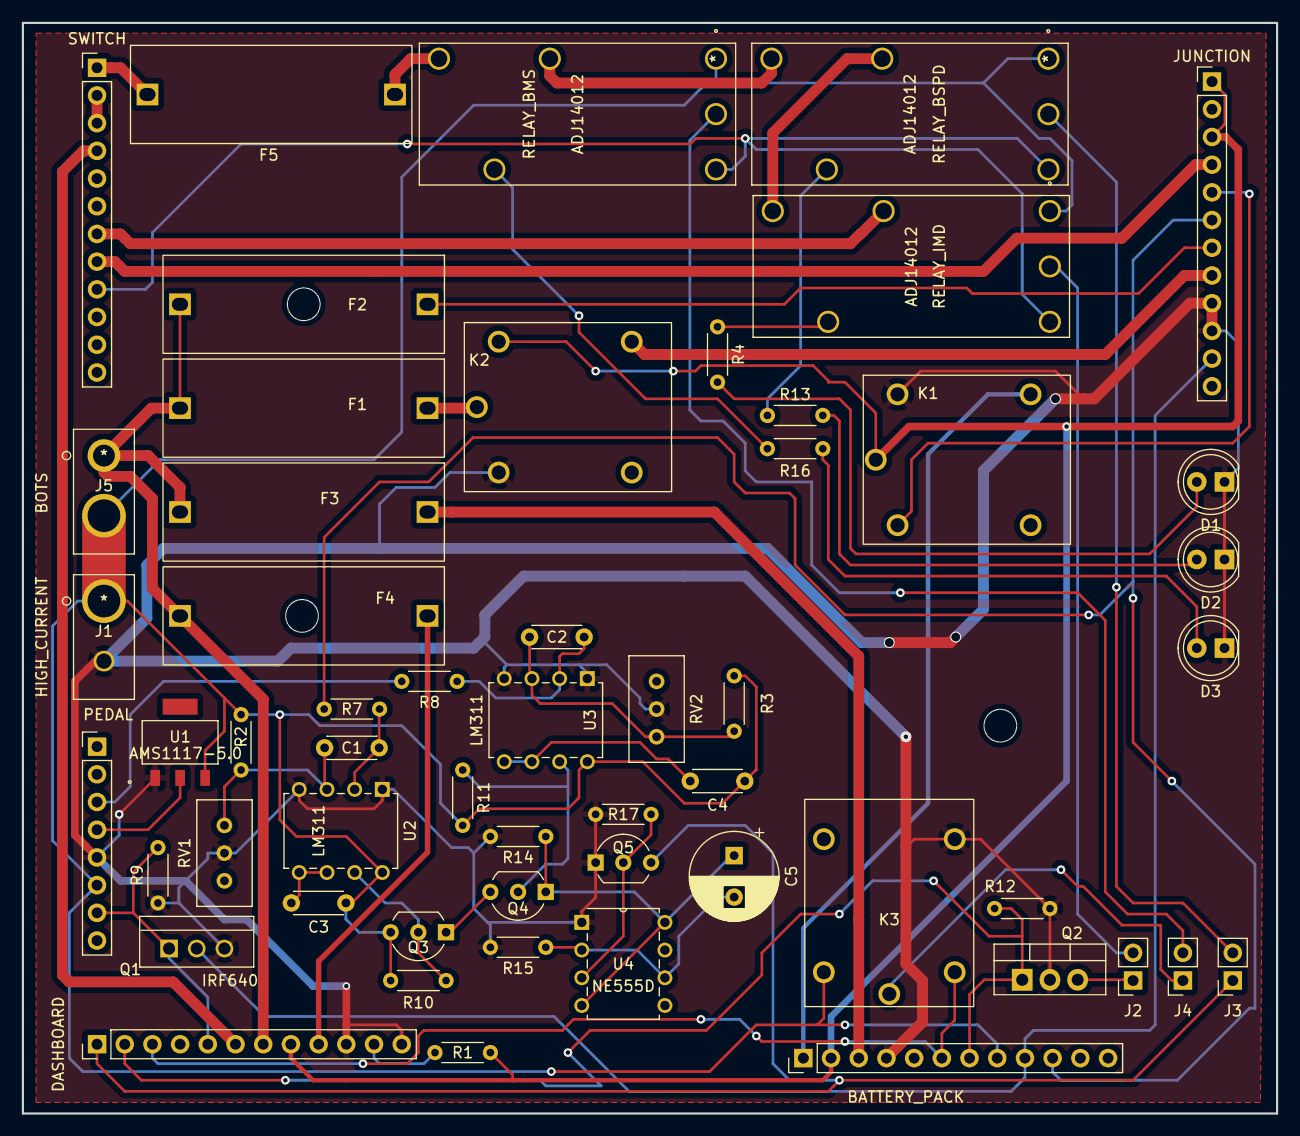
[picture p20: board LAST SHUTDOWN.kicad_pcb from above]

Board: 2 copper layers, 115.0 x 100.0 mm, 55 parts (0 on the bottom side), 52 nets.

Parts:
BATTERY_PACK: Conn_01x12_Male; PinHeader_1x12_P2.54mm_Vertical
C1, C2, C3, C4: 1nF; C_Disc_D4.3mm_W1.9mm_P5.00mm
C5: 10uF; CP_Radial_D8.0mm_P3.80mm
D1, D2, D3: LED; LED_D5.0mm
DASHBOARD: Conn_01x12_Male; PinHeader_1x12_P2.54mm_Vertical
F1, F3, F5: 4A Fuse; 646SERIES_FUSEHOLDER
F2: 1A Fuse; 646SERIES_FUSEHOLDER
F4: 2A Fuse; 646SERIES_FUSEHOLDER
J1: HIGH_CURRENT; 0039281023 5566-02A
J2, J3, J4: Conn_01x02_Male; PinSocket_1x02_P2.54mm_Vertical
J5: BOTS; 0039281023 5566-02A
JUNCTION: Conn_01x12_Male; PinHeader_1x12_P2.54mm_Vertical
K1, K2, K3: HR702NH-DC12V
PEDAL: Conn_01x08_Male; PinHeader_1x08_P2.54mm_Vertical
Q1: IRF640; IRF640NPBF
Q2: IRF9540N; TO-220-3_Vertical
Q3, Q4, Q5: 2N3904; TO-92_Inline_Wide
R1, R4, R9, R10, R11, R12, R13, R16: 10k; R_Axial_DIN0204_L3.6mm_D1.6mm_P5.08mm_Horizontal
R2, R3, R14: 4.7k; R_Axial_DIN0204_L3.6mm_D1.6mm_P5.08mm_Horizontal
R7, R8, R17: 1k; R_Axial_DIN0204_L3.6mm_D1.6mm_P5.08mm_Horizontal
R15: 62k; R_Axial_DIN0204_L3.6mm_D1.6mm_P5.08mm_Horizontal
RELAY_BMS: ADJ14012
RELAY_BSPD: ADJ14012
RELAY_IMD: ADJ14012
RV1, RV2: R_Potentiometer_US; Potentiometer_Bourns_3296W_Vertical
SWITCH: Conn_01x12_Male; PinHeader_1x12_P2.54mm_Vertical
U1: AMS1117-5.0
U2, U3: LM311; LM311P
U4: NE555D; NE555P

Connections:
AIR+_ACTIVE: BATTERY_PACK.1, K1.14
AIR+_ACTIVE_SIG: JUNCTION.5, K1.6
AIR-_ACTIVE: BATTERY_PACK.2, DASHBOARD.8, JUNCTION.1, JUNCTION.3, K1.7, K2.2, R1.1
BMS_FAULT: BATTERY_PACK.6, DASHBOARD.3, K3.6
BMS_HALL: BATTERY_PACK.10, JUNCTION.6, R7.2
BOTS_IN: BATTERY_PACK.8, C3.1, C4.1, J1.1, J5.2, K3.2, PEDAL.6, Q3.3 (C), R2.2, R3.2, R10.1, R11.2, RELAY_BMS.1 (V), RELAY_BSPD.1 (V), RELAY_IMD.1 (V), U1.3 (VI), U2.8 (V+), U3.8 (V+)
BOTS_OUT: DASHBOARD.7, F1.2, F2.2, F3.2, F4.2, J5.1
BRAKE: PEDAL.3, R8.2
BRAKE_GND: BATTERY_PACK.4, D1.1 (K), D2.1 (K), D3.1 (K), DASHBOARD.10, DASHBOARD.12, J1.2, JUNCTION.9, JUNCTION.10, K1.2, K2.6, K3.1, PEDAL.5, Q1.3 (S), Q2.2 (D), Q5.1 (E), R9.1, R12.1, R14.2, R15.2, R17.2, RV1.2, RV2.2, U1.1 (GND), U2.1 (GND), U2.4 (V-), U3.1 (GND), U3.4 (V-), U4.1 (GND)
BRAKE_LIGHT-: BATTERY_PACK.9, JUNCTION.11, Q1.2 (D)
BRAKE_OUT: DASHBOARD.5, PEDAL.7, Q1.1 (G), R9.2
BRAKE_PWR: PEDAL.4, U1.2 (VO)
BSPD_FAULT: DASHBOARD.1, J3.1, Q5.3 (C)
HVD_INTERLOCK_OUT: JUNCTION.4, SWITCH.8
HV_ACTIVE_LED: DASHBOARD.11, R1.2
HV_AUX1_OUT: DASHBOARD.6, SWITCH.4
HV_AUX2_OUT: SWITCH.2, SWITCH.3
HV_AUX3_OUT: F5.1, SWITCH.1
HV_MASTER_OUT: RELAY_IMD.2 (Out), SWITCH.7
IMD_FAULT: BATTERY_PACK.7, DASHBOARD.2, Q2.1 (G), R12.2
LV_ECU: DASHBOARD.9, F4.1
LV_INV: JUNCTION.8, K2.14
LV_PACK: BATTERY_PACK.3, F3.1
LV_TSAL: F2.1, JUNCTION.7
unnamed: C1.1, R7.1, U2.2 (+)
unnamed: C1.2, R2.1, RV1.1, U2.3 (-)
unnamed: C2.1, R8.1, U3.2 (+)
unnamed: C2.2, R3.1, RV2.1, U3.3 (-)
unnamed: C3.2, U2.5 (BAL), U2.6 (STRB)
unnamed: C4.2, U3.5 (BAL), U3.6 (STRB)
unnamed: C5.1, Q4.1 (E), R14.1, U4.4 (R), U4.8 (VCC)
unnamed: C5.2, R15.1, U4.2 (TR), U4.6 (THR)
unnamed: D1.2 (A), R4.2
unnamed: D2.2 (A), R13.2
unnamed: D3.2 (A), R16.2
unnamed: F1.1, K2.7
unnamed: F5.2, RELAY_BMS.4 (12V)
unnamed: J2.1, Q2.3 (S)
unnamed: J2.2, RELAY_IMD.9 (D)
unnamed: J3.2, RELAY_BSPD.9 (D)
unnamed: J4.1, K3.7
unnamed: J4.2, RELAY_BMS.9 (D)
unnamed: Q3.1 (E), Q4.3 (C)
unnamed: Q3.2 (B), R10.2, U2.7
unnamed: Q4.2 (B), R11.1, U3.7
unnamed: Q5.2 (B), R17.1, U4.3 (Q)
unnamed: R4.1, RELAY_IMD.6 (N)
unnamed: R13.1, RELAY_BSPD.6 (N)
unnamed: R16.1, RELAY_BMS.6 (N)
unnamed: RELAY_BMS.2 (Out), RELAY_BSPD.4 (12V)
unnamed: RELAY_BSPD.2 (Out), RELAY_IMD.4 (12V)
SHUTDOWN_RESET: RELAY_BMS.8 (L), RELAY_BSPD.8 (L), RELAY_IMD.8 (L), SWITCH.9

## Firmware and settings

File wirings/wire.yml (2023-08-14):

##########################################################
#                       CONNECTORS                       #
##########################################################
connectors:
  ######################## LV PCB ########################

  LV PCB 1-A:
    <<: *LPT
    pinlabels: [LV_PACK+, LV_PACK-, -, AIR+, AIR-, -, BMS_FAULT, IMD_FAULT, -, ON_COOLING, ON_PUMP, ON_RAD_FAN, ON_BATT_FAN, -, CAN_H_BMS, CAN_L_BMS]

  LV PCB 1-B:
    <<: *LPT
    pinlabels: [FORWARD_ENABLE, BRAKE_SW_INV, REGEN_DISABLE, \PROG_ENA, -, CAN_H_INV, CAN_L_INV, RS232_TX, RS232_RX, -, GND_INV, -, AIR_DRIVE, LV_INV+, LV_INV-, IGNITION]

  LV PCB 1-C:
    <<: *LPT
    pinlabels: [LV_MASTER1, LV_MASTER2, -, HV_MASTER1, HV_MASTER2, -, RESET1, RESET2, CAN_H_LOGGER, CAN_L_LOGGER]

  LV PCB 1-E:
    <<: *LPT
    pinlabels: [GND_DASHBOARD, LATCH_BMS, LATCH_IMD, LATCH_BSPD, -, HV_AUX_C1, HV_AUX_C2, RTD_BUTTON, RTD_LED, -, SW_COOLING, SW_PUMP, SW_RAD_FAN, SW_BATT_FAN, SW_RTD_EN, -, LCD_5V, LCD_SDA, LCD_SCL]

  LV PCB 1-F:
    <<: *LPT
    pinlabels: [LV_JNC+, LV_JNC-, HALL_SIG, HVD1, HVD2, -, BRAKE_LIGHT+, BRAKE_LIGHT-, BRAKE_PWR, BRAKE_SIG, BRAKE_GND, BRAKE_SW1, BRAKE_SW2, BOTS1, -, -, BOTS2, LV_BATT+, LV_BATT-]

  LV PCB 1-G:
    <<: *LPT
    pinlabels: [CAN_H_DEBUG, CAN_L_DEBUG, CAN_GND_DEBUG, -, -, RS232_DEBUG_RX, UART_GND, -, -, -, -, -, -, ESP_TX, STM_TX, RS232_DEBUG_GND, RS232_DEBUG_TX]

  LV PCB 1-H:
    <<: *LPT
    pinlabels: [DIST_FL_PWR, DIST_FL_SIG, DIST_FL_GND, -, SPD_FL_PWR, SPD_FL_SIG, -, DIST_RL_PWR, DIST_RL_SIG, DIST_RL_GND, -, SPD_RL_PWR, SPD_RL_SIG, -, SPK_L+, SPK_L-, -, HV_AUX_L1, HV_AUX_L2]

  LV PCB 1-I:
    <<: *LPT
    pinlabels: [DIST_FR_PWR, DIST_FR_SIG, DIST_FR_GND, -, SPD_FR_PWR, SPD_FR_SIG, -, DIST_RR_PWR, DIST_RR_SIG, DIST_RR_GND, -, SPD_RR_PWR, SPD_RR_SIG, -, SPK_R+, SPK_R-, -, HV_AUX_R1, HV_AUX_R2]


  ######################## HV BATT ########################

  HV BATT 3-A:
    <<: *LPT
    pinlabels: [LV_PACK+, LV_PACK-, AIR+, AIR-, BMS_FAULT, IMD_FAULT, -, ON_COOLING, ON_PUMP, ON_RAD_FAN, ON_BATT_FAN, CAN_H_BMS, CAN_L_BMS, PRECHARGE_DRIVE, -, CHARGE_POWER, CHARGER_SAFETY, CHARGER_INTERLOCK1, CHARGER_INTERLOCK2]

  HV BATT 3-B:
    <<: *LPT
    pinlabels: [LV_TSAL+, LV_PUMP+, LV_PUMP-, -, LV_FAN_L+, LV_FAN_L-, LV_FAN_R+, -, LV_FAN_R-, -, TSAL_GREEN, TSAL_RED]


  ######################## INVERTER ########################

  INVERTER J1:
    <<: *INV_J1

  INVERTER J2:
    <<: *INV_J2


  ######################## JUNCTION ########################

  JUNCTION 5-A:
    <<: *2p
    pinlabels: [TSMP+, TSMP-]

  JUNCTION 5-B:
    <<: *LPT
    pinlabels: [LV_JNC+, LV_JNC-, -, HALL_SIG, -, HVD1, HVD2, -, -, -, -, -, -, -, -, -, -, LV_BATT+, LV_BATT-]


  ####################### DASHBOARD ########################

  DASHBOARD:
    <<: *LPT
    pinlabels: [GND_DASHBOARD, LATCH_BMS, LATCH_IMD, LATCH_BSPD, -, HV_AUX_C1, HV_AUX_C2, RTD_BUTTON, RTD_LED, -, SW_COOLING, SW_PUMP, SW_RAD_FAN, SW_BATT_FAN, SW_RTD_EN, -, LCD_5V, LCD_SDA, LCD_SCL]


  ###################### CONTROL BOX #######################

  CONTROL BOX 7-A:
    <<: *2p
    pinlabels: [TSMP+, TSMP-]

  CONTROL BOX 7-B:
    <<: *LPT
    pinlabels: [LV_MASTER1, LV_MASTER2, -, HV_MASTER1, HV_MASTER2, -, RESET1, RESET2, CAN_H_LOGGER, CAN_L_LOGGER, -, -, -, -, -, -, -, -, CHASSIS]


  ##################### CHARGE SHUTDOWN ####################

  CHARGE SHUTDOWN A:
    <<: *LPT
    pinlabels: [-, -, AIR-, -, -, -, -, CHARGE_POWER, LV_PACK-, LV_PACK+, CHARGER_INTERLOCK1, CHARGER_INTERLOCK2, CHARGER_SAFETY, AIR+, -, -, -, IMD_FAULT, -]

  CHARGE SHUTDOWN B:
    <<: *RS232

  ####################### DEBUG PORTS ######################

  DEBUG SERIAL:
    <<: *RS232

  DEBUG CAN:
    <<: *RS232

  DEBUG UART:
    type: jumper
    pincount: 4
    pinlabels: [ESP_TX, ESP_GND, STM_TX, STM_GND]

  ####################### POWER LINES ######################

  BOTS:
    subtype: component
    pinlabels: [BOTS1, BOTS2]

  HV AUX L:
    subtype: component
    pinlabels: [HV_AUX_L1, HV_AUX_L2]

  HV AUX R:
    subtype: component
    pinlabels: [HV_AUX_R1, HV_AUX_R2]

  ####################### OTHER PARTS ######################

  CHASSIS:
    subtype: GND
    pins: [CHASSIS]

  MOTOR:
    subtype: component
    pins: [EXC, GND, SIN, /SIN, COS, /COS, TH1, TH2]

  BRAKE LIGHT:
    subtype: component
    pins: [BRAKE_LIGHT+, BRAKE_LIGHT-]

  BRAKE SWITCH:
    subtype: component
    pins: [BRAKE_SW1, BRAKE_SW2]

  RTD1:
    subtype: component
    pins: [+, -]

  RTD2:
    subtype: component
    pins: [+, -]

  TSAL:
    subtype: component
    pins: [TSAL_POWER, TSAL_HV, TSAL_LV]

  SPK L:
    subtype: component
    pins: [SPK_L+, SPK_L-]

  SPK R:
    subtype: component
    pins: [SPK_R+, SPK_R-]

  PUMP:
    <<: *COOLER
    pins: [LV_PUMP+, LV_PUMP-]

  FAN L:
    <<: *COOLER
    pins: [LV_FAN_L+, LV_FAN_L-]

  FAN R:
    <<: *COOLER
    pins: [LV_FAN_R+, LV_FAN_R-]

  APPS:
    <<: *SENSOR_3p

  RPS FRONT:
    <<: *SENSOR_3p

  RPS REAR:
    <<: *SENSOR_3p
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

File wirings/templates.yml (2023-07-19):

templates:
  -: &LPT
    type: LPT02SE-14-19P(072)(LC)
    subtype: male
    pincount: 19
    pins: [A, B, C, D, E, F, G, H, J, K, L, M, N, P, R, S, T, U ,V]
    hide_disconnected_pins: False
    image:
      src: ../image/lpt.png
      width: 300

  -: &2p
    type: 2p connector system
    subtype: male
    pincount: 2
    pins: [1, 2]

  -: &INV_J1
    type: AMPSEAL 776164-1
    subtype: receptacle
    pincount: 35
    pins: [1, 13, 24, 2, 14, 25, 3, 15, 26, 4, 16, 27, 5, 17, 28, 6, 18, 29, 7, 19, 30, 8, 20, 31, 9, 21, 32, 10, 22, 33, 11, 23, 34, 12, 35]
    pinlabels: [XDCR_PWR, AIN1, AIN2, AGND, XDCR_PWR, AIN3, AIN4, AGND, XDCR_PWR, AOUT, AIN6, RLY6, RTD1, AGND, XDCR_PWR, RTD2, AIN5, RLY5, /PROG_ENA, AGND, DIN1, DIN2, DIN3, DIN4, DIN5, DIN6, DIN7, DIN8, GND, CANA_H, CANA_L, CANB_H, CANB_L, TXD, RXD]
    hide_disconnected_pins: True
    image:
      src: ../image/J1.png
      width: 300

  -: &INV_J2
    type: AMPSEAL 770680-1
    subtype: receptacle
    pincount: 23
    pins: [1, 9, 16, 2, 10, 17, 3, 11, 18, 4, 12, 19, 5, 13, 20, 6, 14, 21, 7, 15, 22, 8, 23]
    pinlabels: [XDCR_PWR, ENCA, ENCB, ENCZ, GND, EXC, GND, SIN, /SIN, COS, /COS, GND, -, -, -, GND, GND, RLY1, RLY2, RLY3, RLY4, BATT+, BATT-]
    hide_disconnected_pins: True
    image:
      src: ../image/J2.png
      width: 300

  -: &RS232
    type: RS232
    subtype: female
    pincount: 9
    pins: [1, 2, 3, 4, 5, 6, 7, 8, 9]
    pinlabels: [DCD, RXD, TXD, DTR, GND, DSR, RTS, CTS, RI]
    hide_disconnected_pins: True
    image:
      src: ../image/rs232.png
      width: 300

  -: &SENSOR_3p
    subtype: sensor
    pincount: 3
    pins: [1, 2, 3]
    pinlabels: [VCC, SIG, GND]

  -: &SENSOR_2p
    subtype: sensor
    pincount: 2
    pins: [1, 2]
    pinlabels: [VCC, SIG]

  -: &COOLER
    subtype: cooler
    pincount: 2
    pins: [1, 2]


  -: &wire
    category: bundle
    gauge: 22 AWG
    show_equiv: True
    colors: [RD, BK, WH, GY, GN, BU, VT, BN]
    # RED, BLACK, WHITE, GREY, GREEN, BLUE, VIOLET, BROWN

  -: &sensorwire_3p
    <<: *wire
    colors: [RD, GN, BK]

  -: &sensorwire_2p
    <<: *wire
    colors: [RD, GN]

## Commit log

2023-03-01 update schematics snapshot
    [CHARGE SHUTDOWN.kicad_sch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]
2023-07-19 update: schematics and wirings to current state
    [CHARGE_SHUTDOWN.csv, CHARGE_SHUTDOWN.kicad_sch, CONTROL.kicad_sch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]
2023-08-12 refactor: 23/08/13 new LV PCB
    [LV_PCB-B_Cu.gbr, LV_PCB-B_Mask.gbr, LV_PCB-B_Paste.gbr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]
2023-08-12 update: 23/08/13 current wiring system
    [wire.bom.tsv]
2023-08-14 update: 23/08/14
    [CHARGE_SHUTDOWN-B_Cu.gbr, CHARGE_SHUTDOWN-B_Mask.gbr, CHARGE_SHUTDOWN-B_Silkscreen.gbr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]
2023-08-14 fix: broken LV_PCB link
    [CONTROL.kicad_sch, DASHBOARD.kicad_sch, EV.kicad_sch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]

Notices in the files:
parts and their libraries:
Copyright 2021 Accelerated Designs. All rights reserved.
